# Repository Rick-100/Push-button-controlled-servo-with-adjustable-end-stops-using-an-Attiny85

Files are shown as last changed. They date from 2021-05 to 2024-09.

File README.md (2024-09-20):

# Push-button-controlled-servo-with-adjustable-end-stops-using-an-Attiny85

This repository is for this video:

https://youtu.be/g3QAqGpAoNo

This program is written for the Attiny85. It moves a servo between 2 end positions using two push buttons. The end positions are adjustable by using a program mode selected by a third button. The positions are stored in eeprom so they are not lost on power down. If the circuit is powered on with the program button held down, the default values are restored. The project was started after watching this video by pileofstuff:

https://youtu.be/vMrGfrk_M0I

The video is about controlling the track switches on a model train layout with either push buttons or IR sensors. The push buttons are for manual control. The IR sensors detect a train coming and set the switch in the direction that won't derail the train. The end positions of the servos need to be adjustable so the servo doesn't bind. In the video he used pots on an Arduino Nano to set the end positions. The push buttons and IR sensors were wired in parallel. While reading the video comments, people suggested using this method so I thought I would give it a try on the Attiny85 to get some more experience with the chip. I'm also designing an experimenters board for the Attiny85 and needed a project to test it out.

The program uses the Arduino IDE and this core:

https://github.com/SpenceKonde/ATTinyCore

While the program uses the Arduino IDE, I started development with Atmel Studio 7. That's why the code looks a little different than most Arduino code. I did not use the Arduino methods of manipulating the pins. When compiling and burning the code use the following settings in the IDE:

 *  Attiny is running at 8 MHz internal
 *  Timer 1 clock: CPU frequency
 *  millis() micos(): disabled
 *  Save eeprom: eeprom not detained
 *  B.O.D. disabled
 *  

The interrupt driven servo routines are a modified version of routines from this program by Andreas Ennemoser:

https://github.com/chiefenne/ATTINY85-Servo-Control/blob/master/main.c

I modified them to get more servo travel at the price of some resolution:

 *defaults servo positions servo operates between 2 and 187
 *pulse lengths between approximately 750uS and 2250 uS

Most of the program is taken up by the user interface. Since the servo refresh rate is approximately 50 Hz, the main loop is synced to the refresh. The program uses 4 modes to keep track of what it's doing:

 * the user interface is 3 pushbuttons PLUS   PROG    MINUS and an led
 * 
 * mode 0 = solid led / normal running mode 
 *  pressing PLUS moves the servo end PLUS end position
 *  pressing MINUS moves the servo end MINUS end position
 * 

 * mode 1 = slowest flashing led  
 *  the prog button was pressed and it's waiting for a press on PLUS or MINUS to select which end to adjust
 * the servo will move to the initial position stored in variables plus_limit or minus_limit and enter mode 2
 * 

 * mode 2 = faster flashing led / the servo positions are adjusted until PROG is pressed and released  
 *  then there stored in eeprom and mode 0 is entered
 *

 *mode 3 = even faster flashing led on power up / the eeprom was read and the data was out of range or bad checksum 
 *  the limits were restored to defaults but not written to eeprom
 *  when the PROG button is pressed and released the data is written to eeprom and mode is set to 0
 *  back to solid led
 *

 *mode 4 = fastest flashing led / happens after aprox 10 seconds of no buttons pressed 
 *  servos pulses have been disabled so the servo is no longer actively driven
 *  pressing PLUS or MINUS enables the servo pulses and puts mode back to 0 with solid led
 *  pressing and releasing PROG enables servo pulses and puts mode back to 0 with solid led
 * 
 * 
 *to reset to values stored in constants MAXPLUS and MAXMINUS power up with PROG button held down
 * 

In his video pileofstuff showed the push buttons and IR sensors wired in parallel. When I was testing the circuit with the sensors , if a sensor was blocked it interferes with the push button. This could probably be fixed by adding a spdt toggle switch on each Attiny85 pin that the buttons are on. The toggle switch could select either the button or the sensor to connect to the pin. 

This has been a fun project even though I'm not into model trains. I think it might be useful for other non train projects. The code is a starting point for another project I have in mind. I've been using my 3018 CNC to make boards with the isolation routing method, so I designed some circuit boards for the project. I'll include the gerber files in case anyone wants them. There are two boards. The one with the Attiny85 and the one that has the push buttons and led. The attiny board has headers for connecting the IR sensors. The sensors have a non standard pinout but the board uses the hobby servo standard of 1:GND 2:V+ 3:SIG so you have to swap the wire in the hook up wires you use.

You can go here to open the board in the Easyeda editor.
https://oshwlab.com/Rick100/servo_limit_est_sw

The small user input board:
https://oshwlab.com/Rick100/servo_limits_user

I added the servo_limits_speed.ino to give the option of controlling the speed the servo moves.

Thanks

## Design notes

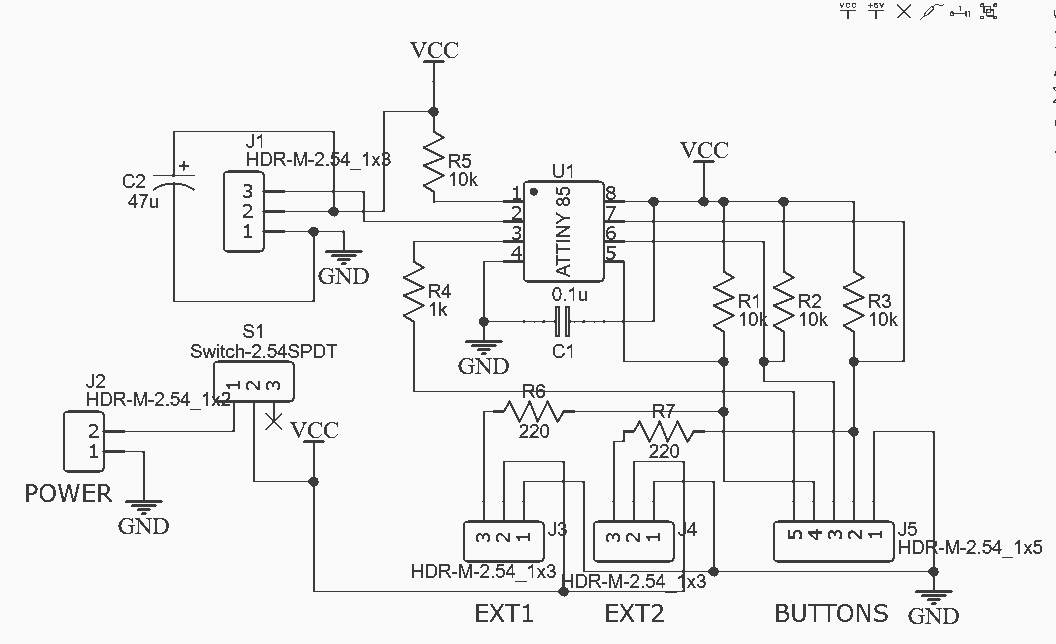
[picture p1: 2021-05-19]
Images/main_board.png

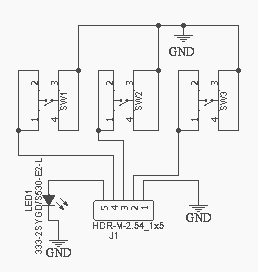
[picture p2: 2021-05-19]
Images/input_board.png

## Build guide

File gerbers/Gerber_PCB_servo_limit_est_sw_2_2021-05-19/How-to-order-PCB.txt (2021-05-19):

How to Order PCB

Please refer to:
https://docs.easyeda.com/en/PCB/Order-PCB

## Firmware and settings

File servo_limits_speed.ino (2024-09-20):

/*
* ATTINY85 prog to to toggle servo between 2 end positions
* the end positions are adjustable and saved in eeprom so they are not lost when power is turned off
* the user interface is 3 pushbuttons PLUS   PROG    MINUS and an led
* 
* mode 0 = solid led / normal running mode 
*  pressing PLUS moves the servo end PLUS end position
*  pressing MINUS moves the servo end MINUS end position
* 
* mode 1 = slowest flashing led  
* the prog button was pressed and it's waiting for a press on PLUS or MINUS to select which end to adjust
* the servo will move to the initial position stored in variables plus_limit or minus_limit and enter mode 2
* 
* mode 2 = faster flashing led / the servo positions are adjusted until PROG is pressed and released  
*  then there stored in eeprom and mode 0 is selected
*
*mode 3 = even faster flashing led on power up / the eeprom was read and the data was out of range or bad checksum 
*  the limits were restored to defaults but not written to eeprom
*  when the PROG button is pressed and released the data is written to eeprom and mode is set to 0
*  back to solid led
*
*mode 4 = fastest flashing led / happens after aprox 10 seconds of no buttons pressed 
*  servos pulses have been disabled so the servo is no longer actively driven
*  pressing PLUS or MINUS enables the servo pulses and puts mode back to 0 with solid led
*  pressing and releasing PROG enables servo pulses and puts mode back to 0 with solid led
* 
*
*to reset to values stored in constants MAXPLUS and MAXMINUS power up with PROG button held down
*
*Programming settings  in Arduino IDE ver 1.8.12
*  Attiny is running at 8 MHz internal
*  Timer 1 clock: CPU frequency
*  millis() micos(): disabled
*  Save eeprom: eeprom not detained
*  B.O.D. disabled
*  
*  PB1 (leg 6) PROG button
*  PB2 (leg 7) PLUS
*  PB0 (leg 5) MINUS
*  PB3 (leg 2) servo
*  PB4 (leg 3) led
*
*The interrupt driven servo routines are a modified version of routines from this program
*by Andreas Ennemoser
*https://github.com/chiefenne/ATTINY85-Servo-Control/blob/master/main.c
*
*
*
*
*This version has a servo_speed variable. It will slow the servo down when it's in the mode 0 (running mode)
*The servo still moves at full speed in other modes when your adjusting the end points. I tested the values 1 , 3 , and 50.
*A value of 1 is the slowest. A value of 50 seems to be full speed. A value of 0 results in no movement.
*/

#include <EEPROM.h>

#define SERVO PB3   // define pin where servo is attached (one of PB0, PB1, PB2, PB3, PB4)
#define LED PB4

#define BUTTONPLUS PINB2  //buttons
#define BUTTONMINUS PINB0
#define BUTTONPROG PINB1

#define MODE0RATE 0   // blink rates for the modes lower number = faster blink / 0 = no blink
#define MODE1RATE 20
#define MODE2RATE 10
#define MODE3RATE 5
#define MODE4RATE 1

#define TIMEOUT 500 //.02 * 500 = 10 seconds



//defaults servo positions servo operates between 2 and 187
//pulse lengths between approximately 750uS and 2250 uS
//ex: to convert 187 to pulse length
//each timer tick is 1/8000000 * 64 or .000008 seconds  / 64 is the prescaler
//multiply .000008 by 187 to get .001496 seconds
// add it to the base of .000750 seconds to get .002246 or 2246 uS
#define MAXPLUS 187 
#define MAXMINUS 2  
#define POSMID 93

//#define SELECTPLUS 140  // initialpositions for servo adjust 
//#define SELECTMINUS 46



#define SERVO_PWM_ON PORTB |= (1 << SERVO)
#define SERVO_PWM_OFF PORTB &= ~(1 << SERVO)
//#define LED_ON PORTB |= (1 << LED)
//#define LED_OFF PORTB &= ~(1 << LED)
#define LED_OFF PORTB |= (1 << LED)
#define LED_ON PORTB &= ~(1 << LED)
#define LED_TOGGLE PORTB ^= (1<< LED)

// global variables

volatile uint8_t overflows = 0;              // number of timer1 overflows (0-255)

volatile uint8_t servo_pos;     
volatile bool ok_change; // set when timer starts it's 20 mS phase
volatile bool servo_enable;  //if true drive the servo

uint8_t plus_limit;
uint8_t minus_limit;

uint16_t jiffy_clock; // keeps track of 50 Hertz ticks

uint8_t servo_speed = 3; // number of 'steps' the servo moves on each jiffy clock tick/ 1 - 50 seem to work well /  don't use 0


ISR(TIMER1_OVF_vect){

	// interrupt service routine for timer1 overflow
	// 1 interrupt is approx. 2ms

	overflows++;
	
	if (overflows == 10){                    // corresponds to approx 20ms servo frequency (50Hz) .02048 seconds
		if(servo_enable)
		{
			SERVO_PWM_ON;
		}
		//SERVO_PWM_ON;
		TCNT1 = 162;  // set up base .000750 sec pulse*****  (.000750 / (64 * (1/8000000)) = 93.75) ****** 256 - 94 = 162
	}

	if (overflows == 11){                     // corresponds to 1ms servo pulse minimum
		//flag = 1;
		overflows = 0;
		// adds in the compare B match interrupt ISR the remaining part of servo pulse on top of this minimum 1ms pulse
		// can be anything between 0ms and 1ms (or 0-255 steps according to timer1 setup)
		//OCR1B = servo_pwm_duty_int;          // set Timer/Counter1 Output Compare RegisterB (datasheet page 91)
		OCR1B = servo_pos;          // set Timer/Counter1 Output Compare RegisterB (datasheet page 91)
		//TCNT1 = 0;                           // reset counter for the upcoming match with OCR1B
		TIFR |= (1 << OCF1B); // clear the interrupt flag by writing a one to it
		TIMSK |= (1 << OCIE1B);                  // enable compare match B interrupt of timer1 (page 92)
	}

}

ISR(TIMER1_COMPB_vect){

	// interrupt service routine for timer1 compare match based on OCR1B value
	// this match happens anywhere between 1ms and 2ms after SERVO_PWM_ON
	SERVO_PWM_OFF;
	TIMSK &= ~(1 << OCIE1B);                  // disable compare match B interrupt of timer1 (page 92)
	ok_change = true;    // signal foreground program it's time
}


void Init_PORT(void)
{
	DDRB |= (1 << SERVO);     // set servo pin as output
	DDRB |= (1 << LED);     // set led pin as output
	//PORTB |= (1 << BUTTONPLUS);   //turn on pullups
	//PORTB |= (1 << BUTTONMINUS);
	//PORTB |= (1 << BUTTONPROG);

}

void Init_TIMER()
{

	// this function initializes the timer
	// the timer is set up in order to last approx. 1ms per overflow
	// the CPU runs at 8MHz (requires that CKDIV8 fuse is NOT set)
	// timer 1 is used as it allows for more prescalers; here 32 is used to come from 8MHz to 250kHz

	TCCR1 |= (1 << CS12) | (1 << CS11) | (1 << CS10);      // set prescaler of timer1 to 64


}

void Init_INTERRUPTS()
{
	// this function initializes the interrupts
	TIMSK |= (1 << TOIE1);                   // enable overflow interrupt of timer1 (page 92)
	// did not work with OCIE1A???
	//TIMSK |= (1 << OCIE1B);                  // enable compare match B interrupt of timer1 (page 92)
	sei();                                   // enable interrupts (MANDATORY)

}

void storeValues()
{
	uint8_t checksum;

	checksum = plus_limit + minus_limit;
	EEPROM.write(0,(int)plus_limit);
	//EEPROM.write(0,0);
	EEPROM.write(1,(int)minus_limit);
	//EEPROM.write(1,0);
	EEPROM.write(2,(int)checksum);
}

bool loadValues()
{
	uint8_t checksum;
	uint8_t temp;

	plus_limit = EEPROM.read(0);
	minus_limit = EEPROM.read(1);
	checksum = EEPROM.read(2);
	temp = plus_limit + minus_limit;
	if(checksum == temp)
	{
		return false; //ok
	}
	else
	{
		return true; //error
	}

}

void startServoPulses()
{
	Init_TIMER();                            // initialize timer
	Init_INTERRUPTS();                       // initialize interrupts

}

void stopServoPulses()
{
	cli();
}

void setup() {
	// put your setup code here, to run once:

}

void loop() {

	uint8_t mode;
	uint8_t blink_rate;
	uint8_t blink_count;
	uint8_t limit_sel;


	uint16_t current_servo_pos; //
	uint8_t target_servo_pos;  //

	bool prog_pushed;      //for detecting when PROG button has been pressed and released
	bool prog_released;
	bool moving = false;    // true if servo is in process of moving between positions

	prog_pushed = false;
	prog_released = false;

	mode = 0;   //normal mode
	blink_rate = 0;
	blink_count = 0;
	limit_sel = 0;
	jiffy_clock = 0;
	LED_ON;   //turn on led

	ok_change = false;  //set at start of timer 20 mS timer phase to allow foreground task to chnage both bytes of servo_pos

	Init_PORT();

	if((PINB & (1 << BUTTONPROG)) == 0) // restore default limits if powered up with PROG button down
	{
		plus_limit = MAXPLUS;
		minus_limit = MAXMINUS;
		storeValues();
		while ((PINB & (1 << BUTTONPROG)) == 0);  //wait until PROG button released
	}
	else
	{
		if(loadValues())  //load data from eeprom
		{
			plus_limit = MAXPLUS;   //error
			minus_limit = MAXMINUS;
			mode = 3;
			blink_rate = MODE3RATE;      
		}
		if((plus_limit > MAXPLUS) || (plus_limit < MAXMINUS))  //if either value is out of range restore both and put in error mode 3
		{
			plus_limit = MAXPLUS;
			minus_limit = MAXMINUS;
			mode = 3;
			blink_rate = MODE3RATE;
		}
		if((minus_limit < MAXMINUS) || (minus_limit > MAXPLUS))
		{
			plus_limit = MAXPLUS;
			minus_limit = MAXMINUS;
			mode = 3;
			blink_rate = MODE3RATE;
		}
		
	}
	//-----------------------------------------------------------------------------------
	servo_enable = true;
	//servo_pos = minus_limit;
	servo_pos = POSMID;
	current_servo_pos = POSMID;
	target_servo_pos = servo_pos;
	startServoPulses();

	while(1)
	{
		if(ok_change) //wait until interrupt flags that the 19mS low period of the servopulse has started approx 50 Hz
		{
			ok_change = false;  //reset the flag
			jiffy_clock++;
			if(jiffy_clock > TIMEOUT)
			{
				mode = 4;
				blink_rate = MODE4RATE;
				blink_count = 0;
				servo_enable = false;
			}
			if((PINB & (1 << BUTTONPROG)) == 0) //is PROG button down
			{
				prog_pushed = true;  // flag that it's been down
			}
			else
			{
				if(prog_pushed == true)  // if button was pressed down and is now up
				{
					prog_released = true;  // flag that it has been released
					prog_pushed = false;  //reset the flag
					jiffy_clock = 0;  //reset it
					servo_enable = true;
				}
			}

			
			if(blink_rate)  // blink the led if blink_rate is not 0
			{
				blink_count++;
				if(blink_count == blink_rate)
				{
					//LED = !LED;
					LED_TOGGLE;
					blink_count = 0;
				}
			}
			else  // if blink_rate = 0
			{
				LED_ON;
			}
			
			//--------------------------------------------------------------------------
			
			if(prog_released == true)  // was the PROG button pressed and released
			{
				prog_released = false;
				
				switch(mode)
				{
				case 0:   // put in mode 1 to wait for PLUS or MINUS to be selected
					mode = 1;
					blink_rate = MODE1RATE;
					blink_count = 0;
					break;

				case 2:   //update the variable /store the data in eeprom / go back to mode 0
					if(limit_sel == 0)
					{
						plus_limit = servo_pos;
					}
					else
					{
						minus_limit = servo_pos;
					}

					stopServoPulses();
					storeValues();
					startServoPulses();
					
					mode = 0;
					blink_rate = MODE0RATE;
					blink_count = 0;
					servo_pos = POSMID;
					current_servo_pos = POSMID;
					target_servo_pos = POSMID;
					break;
					
				case 3:       //eeprom read out of range numbers and variables have been restored to defaults
					stopServoPulses();
					storeValues();
					startServoPulses();
					mode = 0;
					blink_rate = MODE0RATE;
					blink_count = 0;
					//LED_ON;
					break;
					
				case 4: //no servo drive mode
					mode = 0;
					blink_rate = MODE0RATE;
					blink_count = 0;
					servo_enable = true;
					//LED_ON;
					break;
					
				default:  //go back to mode 0
					mode = 0;
					blink_rate = MODE0RATE;
					blink_count = 0;
					//LED_ON;
				}
			}
			//------------------------------------------------------------------------------------------     
			// now look at PLUS MINUS buttons 
			switch (mode)
			{
			case 4: //sleep mode so just go back into mode 0 (normal run mode)
				{
					if(((PINB & (1 << BUTTONPLUS)) == 0) || ((PINB & (1 << BUTTONMINUS)) == 0))
					{
						jiffy_clock = 0; //reset on button press
						servo_enable = true;
						mode = 0;
						blink_rate = MODE0RATE;
						blink_count = 0;
					}
					//break;
				}
				
			case 2: //adjust the position
				{ 
					moving = false;
					if((PINB & (1 << BUTTONPLUS)) == 0)         //if PLUS button is pressed and its not moving
					{
						jiffy_clock = 0; //reset
						servo_enable = true;  //make sure output is enabled
						servo_pos++;
						if(servo_pos > MAXPLUS) // constrain to limits
						{
							servo_pos = MAXPLUS;
						}
					}
					else if((PINB & (1 << BUTTONMINUS)) == 0)
					{
						jiffy_clock = 0; //reset
						servo_enable = true;  //make sure output is enabled
						servo_pos--;
						if(servo_pos < MAXMINUS)// constrain
						{
							servo_pos = MAXMINUS;
						}
					}
					break;
				}

			case 1: //select which limit were adjusting and put in mode 2
				{
					moving = false;
					if((PINB & (1 << BUTTONPLUS)) == 0)       //if PLUS button is pressed
					{
						mode = 2;
						blink_rate = MODE2RATE;
						blink_count = 0;
						limit_sel = 0;
						servo_pos = plus_limit;
						//servo_pos = SELECTPLUS; // move to initial adjust position

					}
					else if((PINB & (1 << BUTTONMINUS)) == 0) //if MINUS button is pressed
					{
						mode = 2;
						blink_rate = MODE2RATE;
						blink_count = 0;
						limit_sel = 1;
						servo_pos = minus_limit;
						//servo_pos = SELECTMINUS; // move to initial adjust position
					}
					break;
				}
				

			case 0: // normal running mode
				{

					if((PINB & (1 << BUTTONPLUS)) == 0)       //if PLUS button is pressed
					{
						jiffy_clock = 0; //reset
						servo_enable = true;  //make sure output is enabled
						current_servo_pos = servo_pos;
						target_servo_pos = plus_limit;
						
					}
					else if((PINB & (1 << BUTTONMINUS)) == 0) //if MINUS button is pressed
					{
						jiffy_clock = 0; //reset
						servo_enable = true;  //make sure output is enabled
						current_servo_pos = servo_pos;
						target_servo_pos = minus_limit;
					}
					
					if(servo_pos != target_servo_pos)
					{
						moving = true;
						if(current_servo_pos < target_servo_pos)  // do we need to move servo in plus direction
						{
							//current_servo_pos++;
              if((target_servo_pos - current_servo_pos) >= servo_speed) // make sure we don't overflow or underflow
              {
							  current_servo_pos = current_servo_pos + servo_speed;
              }
              else
              {
                current_servo_pos = target_servo_pos;
              }
						}
           
						if(current_servo_pos > target_servo_pos)
						{
							//current_servo_pos--;
              if((current_servo_pos - target_servo_pos) >= servo_speed) // make sure we don't overflow or underflow
              {
                current_servo_pos = current_servo_pos - servo_speed;
              }
							else
              {
                current_servo_pos = target_servo_pos;
              }
						}
					}
					else
					{
						moving = false;  
					}
					servo_pos = current_servo_pos;
					

				}
			}
			

		}

	}


}
